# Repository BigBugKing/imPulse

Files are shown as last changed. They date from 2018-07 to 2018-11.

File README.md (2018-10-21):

# Important Notice
This is an open project, so...WORK IN PROGRESS! You might find bugs and incomplete work all over this repository. Therefore, I kindly ask you to keep calm and inform me if you encounter any issue. Thank you!

This project is licensed under the terms of the GNU General Public License v3.0

# What is imPulse?
Energy harvesting alternative for bikes including data logging, smart illumination system and Power Distribution Board for powerbanks

# Description

The aim of this project is to provide a cost-effective alternative to power generation on bikes using conventional stepper motors while adding other capabilities, such as: 

- An integrated data logging system to monitor power generated on each trip. 

- A smart lighting system with addressable LEDs, working as indicators, braking lights and headlights, incorporating Light Dependant Resistors (LDRs) to sense the environment and to reduce the risk of glare. 

- Power Distribution Board (PDB) to charge two different/generic powerbanks. While one powerbank is charged, the other one is used to supply energy to the system. 

Please bear in mind that I am currently testing quick prototypes that may compromise the bike reliability in some cases (aka 'learn by doing'). No stress, compression, bending or torsion analysis have been carried out yet on the power generation stage, so use all this project content at your own risk. 

# Milestones for Hackaday 2018

- Power Generation Stage (Closed)
- Data Logger Stage (Closed)
- Smart Lighting System (Closed)
- eBox Stage (Closed)
- Wiring Harness Stage (Closed)

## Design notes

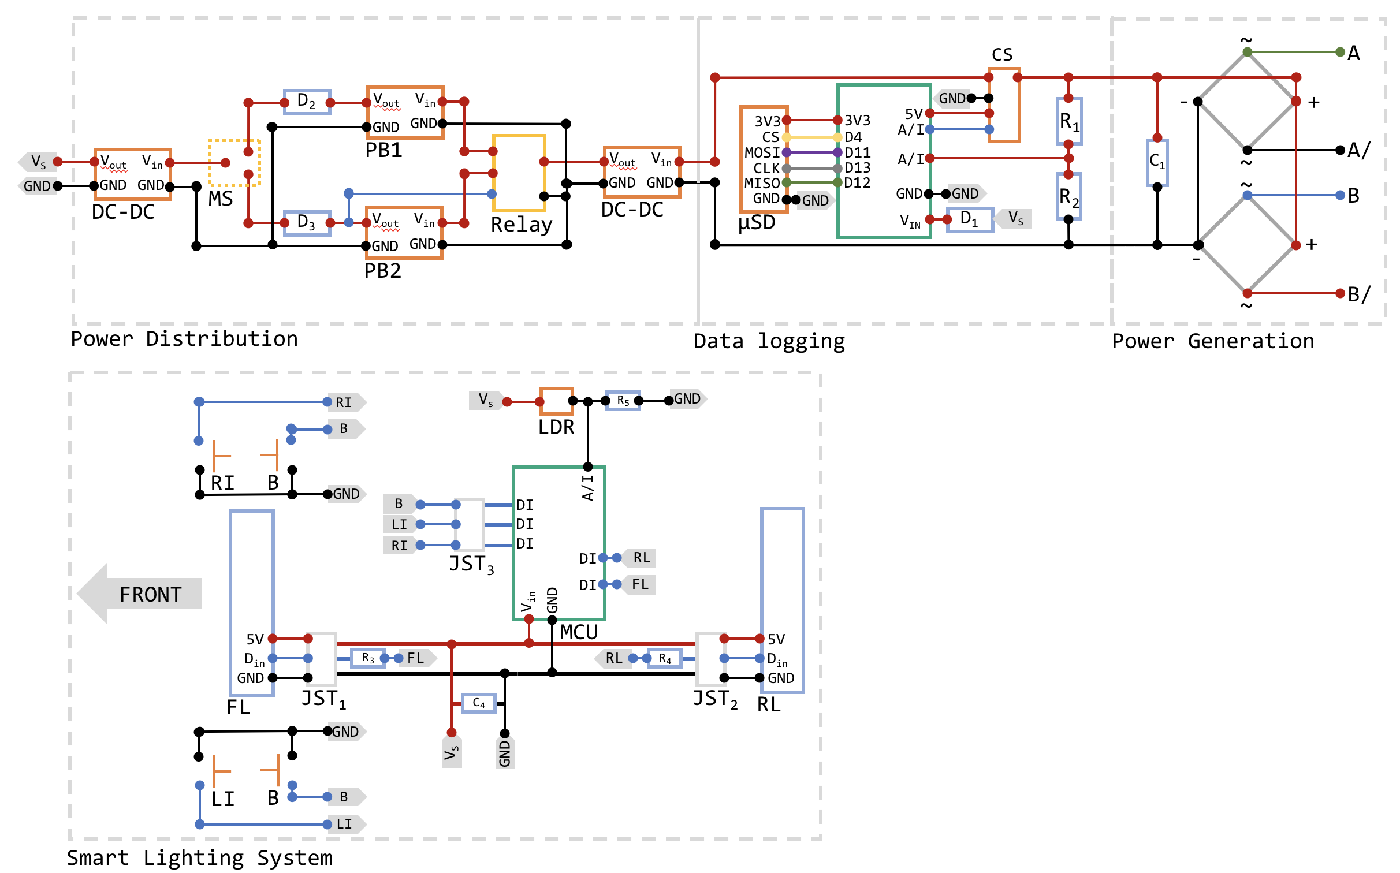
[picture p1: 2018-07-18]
Diagrams/SystemIntegrationStage_v1.png

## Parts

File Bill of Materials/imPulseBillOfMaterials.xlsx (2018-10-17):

Power Generation Stage
Item | Description | Company | Price/Unit | Units | Total | Total + VAT
Stepper Motor | Nema 17 2 Phase 4-wire Stepper Motor 1.8 Degree for 3D Printer (42 x 42 x 34mm) (https://www.amazon.co.uk/Phase-4-wire-Stepper-Degree-Printer/dp/B06ZY9G8KG) | Amazon | £9.16 | 1 | £9.16 | £10.99
JSP XPH-4 | 2.54mm JST-XHP 2 / 3 / 4 / 5 Pin housing and Male / Female Pin Head Connector Adapter Plug (600pcs) (https://www.amazon.co.uk/gp/product/B01GZKFML0/ref=oh_aui_detailpage_o00_s00?ie=UTF8&psc=1) | Amazon | £0.02 | 6 | £0.12 | £0.15
M3 screw | M2 M3 M4 Stainless Steel Hex Head Set Screw Bolts and Nuts (1080pcs) (https://www.ebay.co.uk/itm/1080PC-Assortment-M2-M3-M4-Stainless-Steel-Hex-Head-Set-Screw-Bolts-and-Nuts-Kit/263923485964) | eBay | £0.01 | 4 | £0.04 | £0.05
U channel | Aluminium 6000 U Channel (5m length,38.1x19.1x3.2mm) (20cm needed) (https://www.metalswarehouse.co.uk/product/aluminium-channel/?attribute_pa_grade=6000-series) | Metals Warehouse | £0.90 | 1 | £0.75 | £0.90
Spur Gear | 3D-printed Spur Gear (Cost based on Zortrax Suite) | N/A | 0.66 | 1 | £0.66 | £0.66
Pinion Gear | 3D-printed Pinion Gear (Cost based on Zortrax Suite) | N/A | 0.09 | 1 | £0.09 | £0.09
Washer | A2 Stainless Steel M6 washer (10pcs) (https://www.ebay.co.uk/itm/FORM-C-WASHERS-A2-STAINLESS-STEEL-M4-M5-M6-M8-M10-M12-WIDER-LARGER-FLAT-WIDE-RIM/150939016233) | eBay | £0.11 | 6 | £0.68 | £0.81
Full-wave rectifier | Full Wave Bridge Rectifier 2W08M (2pcs) (https://www.ebay.co.uk/itm/W02M-200V-1A-Full-Wave-Bridge-Rectifier-W02M/191971165883) | eBay | £1.65 | 2 | £3.29 | £3.95
Capacitor | 100uF 25v 105c Low ESR (10pcs) (https://www.ebay.co.uk/itm/100uf-25v-105c-LOW-ESR-Size-11-2mmx6mm-Panasonic-EEUFM1E101-x10pcs/301203555992) | eBay | £0.20 | 1 | £0.20 | £0.24
DC-DC converter | DC 6-24V 12V 24V to 5V 3A USB Step Down Converter (https://www.ebay.co.uk/itm/DC-6-24V-12V-24V-to-5V-3A-Car-USB-Charger-Module-Buck-Step-Down-Converter-Phone/401265883616) | eBay | £2.91 | 1 | £2.91 | £3.49
M3 Grub Screw | M3 A2 Steel Allen Grub Screw (M3x3mm) (4pcs) (https://www.ebay.co.uk/itm/360511046069) | eBay | £0.21 | 1 | £0.21 | £0.25
Data Logging Stage
Item | Description | Company | Price/Unit | Units | Total | Total + VAT
MCU | FireBeetle ESP32 IOT Microcontroller (https://shop.pimoroni.com/products/firebeetle-esp32-iot-microcontroller-supports-wi-fi-bluetooth) | Pimoroni | £15.83 | 1 | £15.83 | £19.00
Current Sensor | 30A ACS712 Current Sensor Module (https://www.ebay.co.uk/itm/5A-20A-30A-ACS712-Module-Measuring-Range-Current-Sensor-Hall-Board-Arduino-PI/262759555611) | eBay | £2.67 | 1 | £2.67 | £3.20
Resistor | Carbon Film Resistor (1 KOhm, 1/4W, 0.25W) (10pcs) (https://www.ebay.co.uk/itm/Carbon-Film-Resistors-1-4W-0-25W-Full-Range-of-Values-Various-Pack-Sizes/152059712084) | eBay | £0.04 | 1 | £0.04 | £0.05
Resistor | Carbon Film Resistor (120 Ohm, 1/4W, 0.25W) (10pcs) (https://www.ebay.co.uk/itm/Carbon-Film-Resistors-1-4W-0-25W-Full-Range-of-Values-Various-Pack-Sizes/152059712084) | eBay | £0.04 | 1 | £0.04 | £0.05
Smart Lighting System Stage
LED Matrix | WS2812B Black LED, WS2811 IC Built-in, 5050 SMD, RGB, DC5V (100pcs) (https://www.amazon.co.uk/gp/product/B01DC0J3UM/ref=od_aui_detailpages00?ie=UTF8&psc=1) | Amazon | £15.57 | 1 | £15.57 | £18.68
LDR | GL5528 Light Dependent Resistor/Photoresistor (10pcs) (https://www.ebay.co.uk/itm/10x-LDR-5528-GL5528-Light-Dependent-Resistor-Photoresistor/132685567359) | eBay | £0.08 | 3 | £0.25 | £0.30
Front Light | 3D-printed Front Light Assembly (Cost based on Zortrax Suite) | N/A | £2.94 | 1 | £2.94 | £2.94
Rear Light | 3D-printed Rear Light Assembly (Cost based on Zortrax Suite) | N/A | £1.28 | 1 | £1.28 | £1.28
M3 screw | M2 M3 M4 Stainless Steel Hex Head Set Screw Bolts and Nuts (1080pcs) (https://www.ebay.co.uk/itm/1080PC-Assortment-M2-M3-M4-Stainless-Steel-Hex-Head-Set-Screw-Bolts-and-Nuts-Kit/263923485964) | eBay | £0.01 | 10 | £0.10 | £0.12
JSP XPH-3 | 2.54mm JST-XHP 2 / 3 / 4 / 5 Pin housing and Male / Female Pin Head Connector Adapter Plug (600pcs) (https://www.amazon.co.uk/gp/product/B01GZKFML0/ref=oh_aui_detailpage_o00_s00?ie=UTF8&psc=1) | Amazon | £0.02 | 15 | £0.31 | £0.37
eBox Stage
Item | Description | Company | Price/Unit | Units | Total | Total + VAT
eBox | 3D-printed eBox Assembly(Cost based on Zortrax Suite) | N/A | £3.50 | 1 | £3.50 | £3.50
Power Bank Housing | 3D-printed Power Bank Housing Assembly (Cost based on Zortrax Suite) | N/A | £2.01 | 2 | £4.02 | £4.02
Mounting Bracket | 3D-printed unting Bracket (Cost based on Zortrax Suite) | N/A | £2.38 | 1 | £2.38 | £2.38
Stripboard | Vero PCB Prototyping Board, Strip Board (95x127mm) (https://www.ebay.co.uk/itm/Vero-PCB-Prototyping-Stripboard-Strip-Board-2-54mm-Pitch/282567751352) | eBay | £1.99 | 1 | £1.99 | £2.39
Relay | 5V Mini Songle Relay SPDT 5-Pins PCB (https://www.ebay.co.uk/itm/5V-12V-24V-Mini-Songle-Relay-SPDT-5-Pins-PCB-1st-Class/281769556517) | eBay | £1.24 | 1 | £1.24 | £1.49
Diode | 1N4007 1000V 1A General Purpose Diodes (10pcs) (https://www.ebay.co.uk/itm/10-x-1N4007-1000v-1A-General-Purpose-Diodes-IN4007-1N4000-DO41-UK-Free-Postage/132541781407) | eBay | £0.08 | 2 | £0.17 | £0.20
USB cable | USB 2.0 to MICRO USB Male / Male cable, 1m | eBay | £0.83 | 2 | £1.65 | £1.98
Power Bank | Ultra Slim Emergency Pocket Sized Battery Power Bank (2000mAh, 1A@5V) (https://www.amazon.co.uk/gp/product/B01KN1OV5K/ref=oh_aui_detailpage_o02_s00?ie=UTF8&psc=1) | Amazon | £8.33 | 2 | £16.65 | £19.98
Single Solid Core (SSC) Wire | Black Single Solid Core 1.8A@300V, 22-23 AWG (0.6mm x 1m) (https://www.ebay.co.uk/itm/13m-1-0-6mm-Equipment-Wire-Kit-22-23-AWG-Single-Solid-Core-1-8A-WP-011118/232901568073) | eBay | £0.22 | 1 | £0.22 | £0.26
SSC Wire | Red Single Solid Core 1.8A@300V, 22-23 AWG (0.6mm x 1m) (https://www.ebay.co.uk/itm/13m-1-0-6mm-Equipment-Wire-Kit-22-23-AWG-Single-Solid-Core-1-8A-WP-011118/232901568073) | eBay | £0.22 | 1 | £0.22 | £0.26
SSC Wire | Green Single Solid Core 1.8A@300V, 22-23 AWG (0.6mm x 1m) (https://www.ebay.co.uk/itm/13m-1-0-6mm-Equipment-Wire-Kit-22-23-AWG-Single-Solid-Core-1-8A-WP-011118/232901568073) | eBay | £0.22 | 1 | £0.22 | £0.26
SSC Wire | Yellow Single Solid Core 1.8A@300V, 22-23 AWG (0.6mm x 1m) (https://www.ebay.co.uk/itm/13m-1-0-6mm-Equipment-Wire-Kit-22-23-AWG-Single-Solid-Core-1-8A-WP-011118/232901568073) | eBay | £0.22 | 1 | £0.22 | £0.26
SSC Wire | Orange Single Solid Core 1.8A@300V, 22-23 AWG (0.6mm x 1m) (https://www.ebay.co.uk/itm/13m-1-0-6mm-Equipment-Wire-Kit-22-23-AWG-Single-Solid-Core-1-8A-WP-011118/232901568073) | eBay | £0.22 | 1 | £0.22 | £0.26
SSC Wire | Purple Single Solid Core 1.8A@300V, 22-23 AWG (0.6mm x 1m) (https://www.ebay.co.uk/itm/13m-1-0-6mm-Equipment-Wire-Kit-22-23-AWG-Single-Solid-Core-1-8A-WP-011118/232901568073) | eBay | £0.22 | 1 | £0.22 | £0.26
M3 screw | M2 M3 M4 Stainless Steel Hex Head Set Screw Bolts and Nuts (1080pcs) (https://www.ebay.co.uk/itm/1080PC-Assortment-M2-M3-M4-Stainless-Steel-Hex-Head-Set-Screw-Bolts-and-Nuts-Kit/263923485964) | eBay | £0.01 | 2 | £0.02 | £0.02
Rubber Sheet | Rubber Sheet (250 x 250 x 1.5mm) (https://www.ebay.co.uk/itm/RUBBER-SHEET-VARIOUS-SIZES-X-1MM-TO-25MM-THICKNESS-AVAILABLE/141120177410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) | eBay | £2.33 | 1 | £2.33 | £2.80
M3 Insert | M3 Threaded Brass Insert for Plastic (M3 x 4.1mm) (5pcs) (https://www.ebay.co.uk/itm/THREADED-BRASS-INSERTS-FOR-PLASTIC-SOLID-PRESS-FIT-METRIC-BARBED-M2-M3-M4-M5-M6/192514339545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) | eBay | £0.25 | 2 | £0.50 | £0.60
Magnet Disc | Neodynium Magnet Disc (25pcs) (https://www.ebay.co.uk/itm/Neodymium-Magnets-Super-Strong-Rare-Earth-Magnets-Craft-Disc-N35-N52-3mm-20mm/253320715735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) | eBay | £0.08 | 8 | £0.64 | £0.76
Rod Bar | DIY Model Stainless Steel Round Rod Bar (2x200mm) (2pcs) (https://www.amazon.co.uk/gp/product/B00O9Y1ENA/ref=oh_aui_detailpage_o08_s00?ie=UTF8&psc=1) | Amazon | £1.28 | 1 | £1.28 | £1.54
LED | LED's Pack in Blue, Green, Yellow and White (100pcs) (https://www.ebay.co.uk/itm/5mm-LEDS-Pack-OF-100-20x-Each-of-Red-Blue-Green-Yellow-White-UK-Seller/182307853772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) | eBay | £0.02 | 2 | £0.04 | £0.05
Resistor | Carbon Film Resistor (220 Ohm, 1/4W, 0.25W) (10pcs) (https://www.ebay.co.uk/itm/Carbon-Film-Resistors-1-4W-0-25W-Full-Range-of-Values-Various-Pack-Sizes/152059712084) | eBay | £0.04 | 2 | £0.08 | £0.10
Switch | Heavy Duty ON/OFF/ON Toggle Switch DPDT + Water Cover (https://www.ebay.co.uk/itm/Heavy-Duty-Toggle-Switch-Flick-ON-OFF-ON-Car-Dash-12V-DPDT-Missile-Water-Cover/371767136221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) | eBay | £2.33 | 1 | £2.33 | £2.79
Wiring Stage
Item | Description | Company | Price/Unit | Units | Total | Total + VAT
Heat Shrink | Black Heat Shrink Tube 3:1 with glue (10mm x 1m) (https://www.amazon.co.uk/gp/product/B06WGQMB1Z/ref=oh_aui_detailpage_o00_s00?ie=UTF8&psc=1) | Amazon | £5.83 | 1 | £5.83 | £6.99
Heat Shrink | Black Heat Shrink Tube 3:1 with glue (5mm x 1m) (https://www.amazon.co.uk/gp/product/B06X3WJ894/ref=oh_aui_detailpage_o00_s00?ie=UTF8&psc=1) | Amazon | £3.33 | 2 | £6.66 | £7.99
Silicon Wire | Black Flexible Soft Silicone Wire Cable 22 AWG (5m) (https://www.ebay.co.uk/itm/Flexible-Soft-Silicone-Wire-Cable-10-12-14-16-18-20-22-24-26-28-30-AWG/322860010747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) | eBay | £1.92 | 2 | £3.83 | £4.60
Silicon Wire | Red Flexible Soft Silicone Wire Cable 22 AWG (5m) (https://www.ebay.co.uk/itm/Flexible-Soft-Silicone-Wire-Cable-10-12-14-16-18-20-22-24-26-28-30-AWG/322860010747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) | eBay | £1.92 | 2 | £3.83 | £4.60
Silicon Wire | Blue Flexible Soft Silicone Wire Cable 22 AWG (5m) (https://www.ebay.co.uk/itm/Flexible-Soft-Silicone-Wire-Cable-10-12-14-16-18-20-22-24-26-28-30-AWG/322860010747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) | eBay | £1.92 | 1 | £1.92 | £2.30
Cable ties | Strong Nylon Plastic Cable Ties Zip, Tie Wraps Organizer (200mm x4.8mm) (100pcs) (https://www.ebay.co.uk/itm/200mmStrong-Nylon-Plastic-Cable-Ties-Zip-Tie-Wraps-organizer-4-8mm-Black-100pcs/391121204862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) | eBay | £1.66 | 1 | £1.66 | £1.99
Cable ties | Releasable Cable Ties, Zip Wrap Straps (100mm x 3.6mm)(100pcs) (https://www.amazon.co.uk/gp/product/B01KK0CAMU/ref=oh_aui_detailpage_o00_s00?ie=UTF8&psc=1) | Amazon | £2.49 | 1 | £2.49 | £2.99
 |  |  |  |  | Total: | £145.20

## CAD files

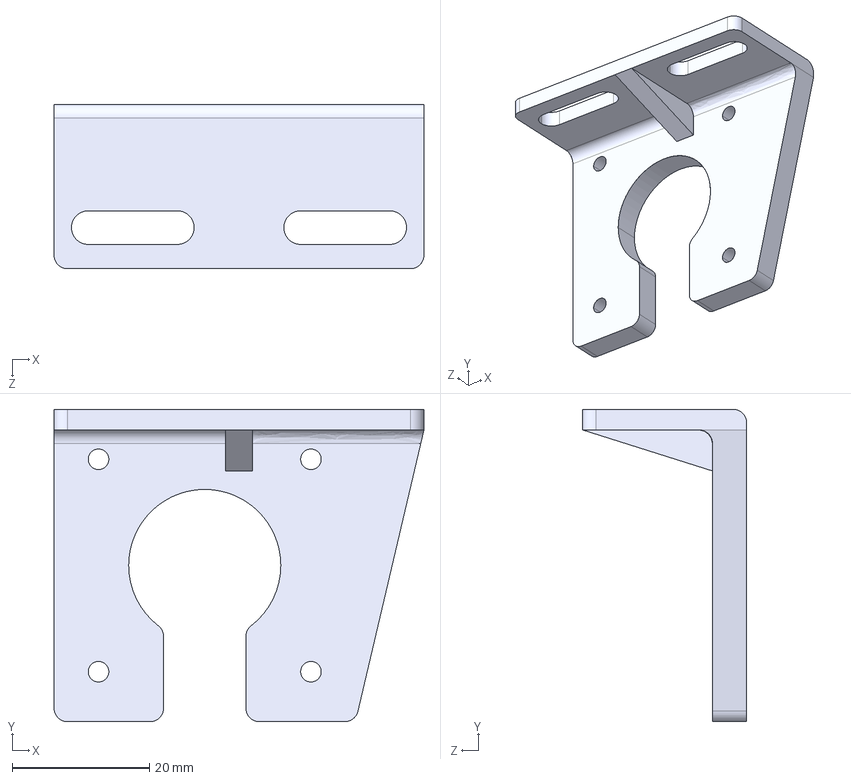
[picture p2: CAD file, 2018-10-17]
CAD/partStepperBracketPlastic.IGS
54.0 x 45.6 x 24.0 mm

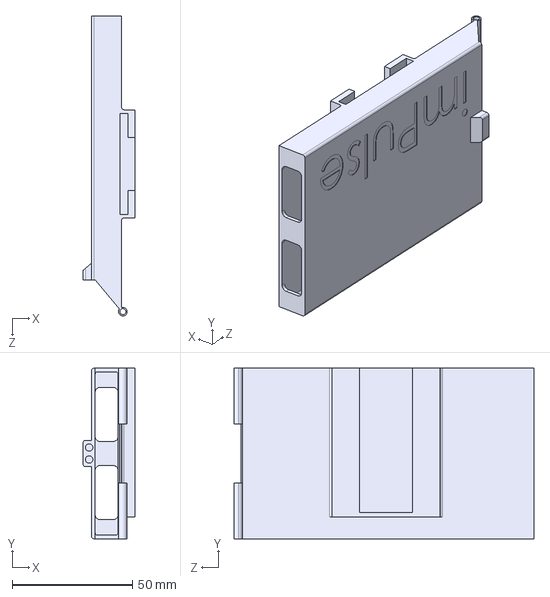
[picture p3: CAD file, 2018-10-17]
CAD/parteBoxBatteryHolderRight.IGS
21.5 x 71.0 x 124.8 mm

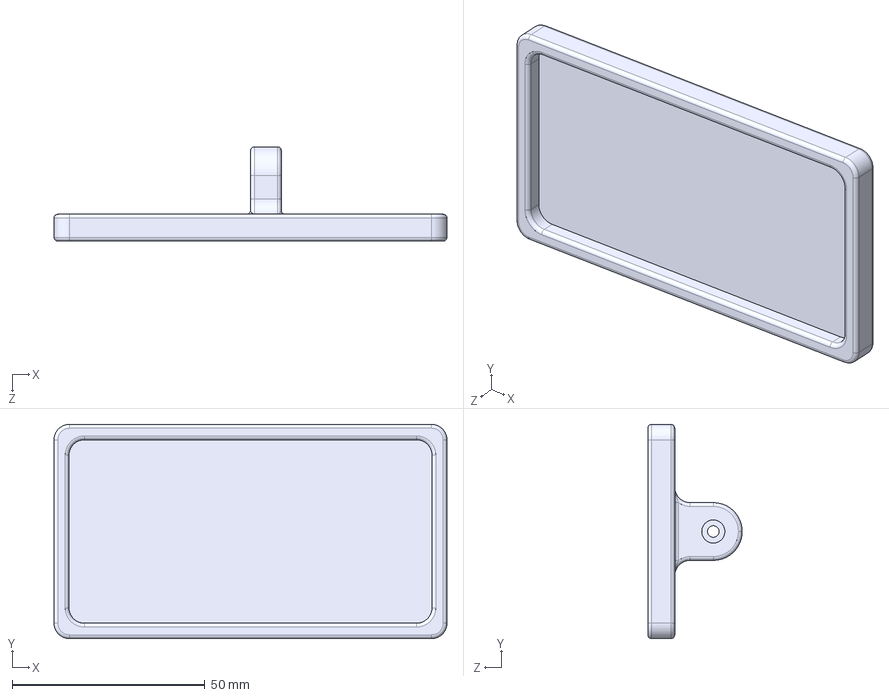
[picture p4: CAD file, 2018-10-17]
CAD/partRearlight.IGS
102.0 x 55.6 x 24.5 mm

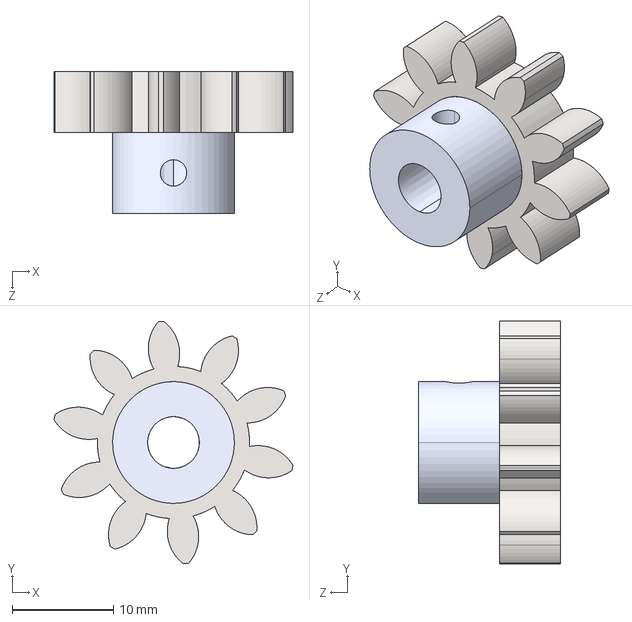
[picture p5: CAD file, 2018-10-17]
CAD/partPinionCustomManufacture.IGS
23.6 x 23.9 x 14.0 mm

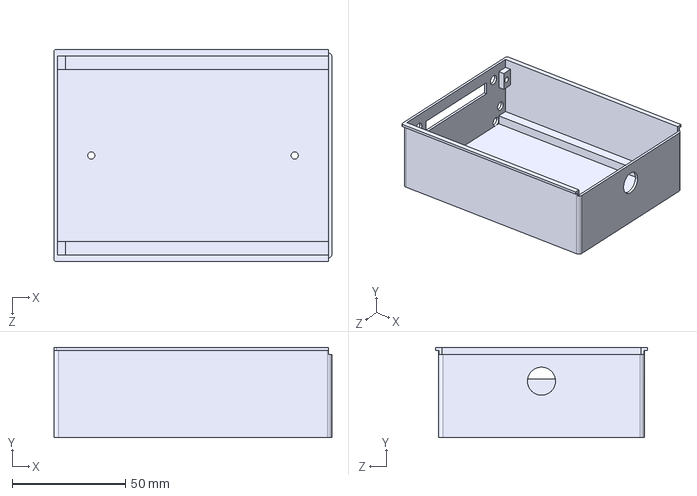
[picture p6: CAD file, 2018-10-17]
CAD/parteBox.IGS
123.0 x 40.0 x 94.0 mm

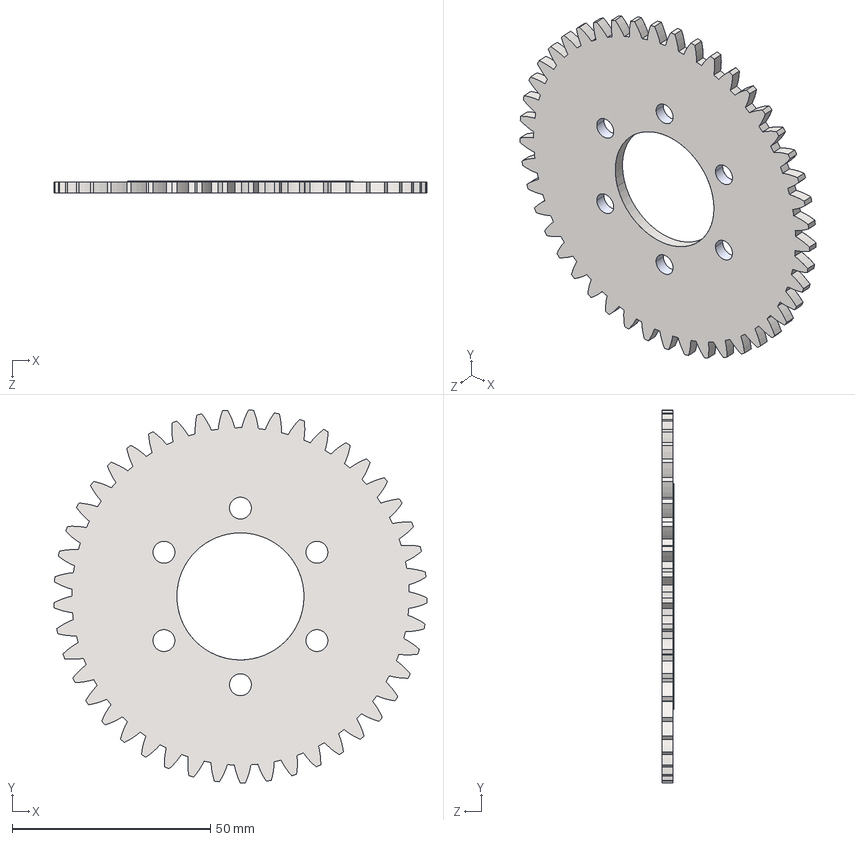
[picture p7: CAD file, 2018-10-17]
CAD/partSpurCustomReinforced.IGS
94.0 x 94.0 x 3.00 mm

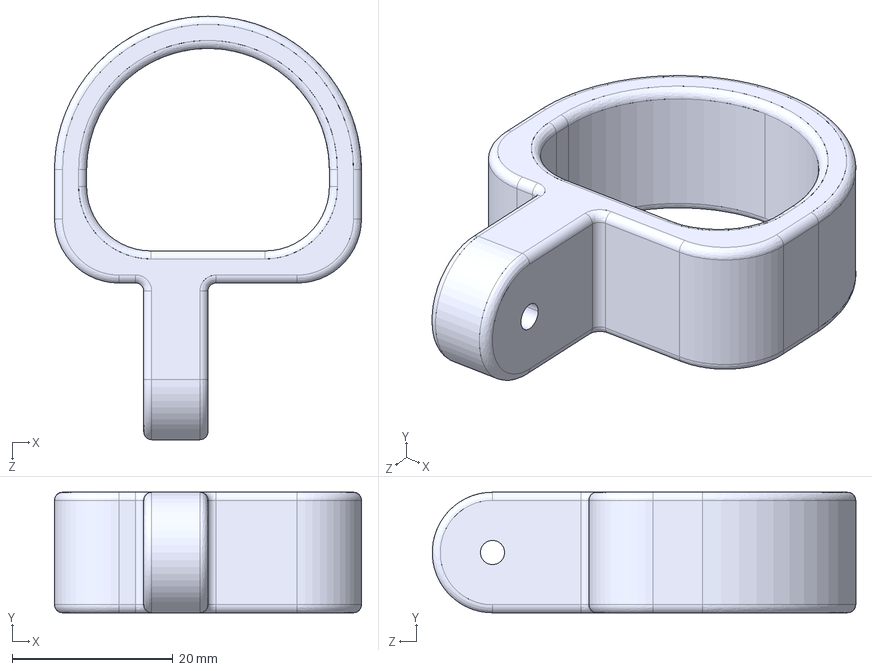
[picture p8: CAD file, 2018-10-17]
CAD/partRearLightSupport.IGS
38.2 x 15.0 x 52.7 mm

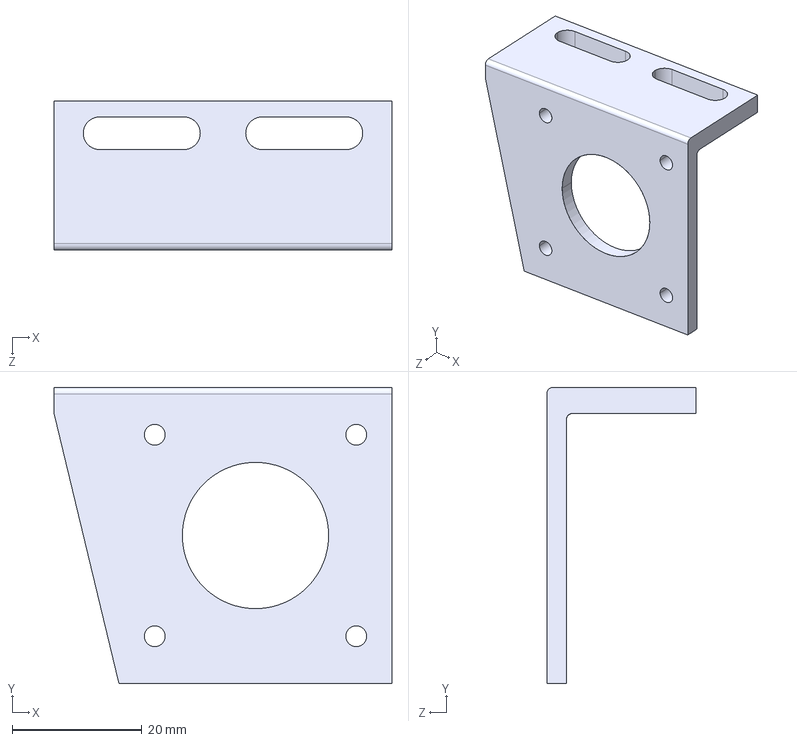
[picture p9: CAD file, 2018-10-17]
CAD/partStepperBracketAl.IGS
52.0 x 45.6 x 23.0 mm

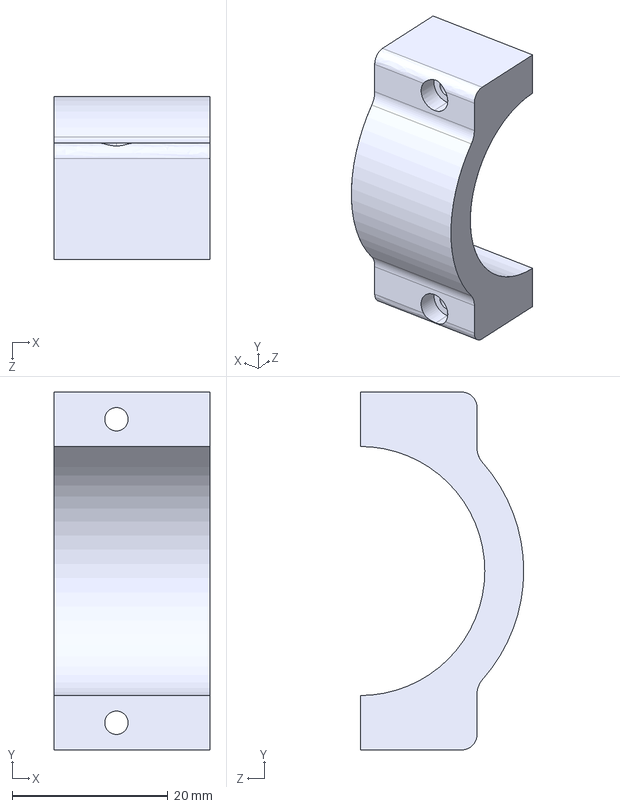
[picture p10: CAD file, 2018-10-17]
CAD/partHeadlightBracket.IGS
20.0 x 46.0 x 21.0 mm

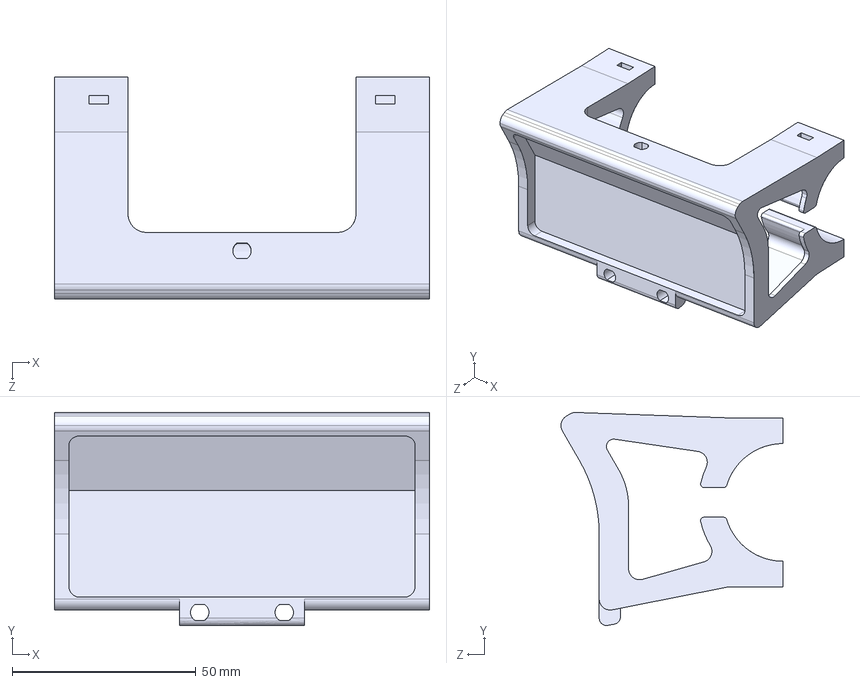
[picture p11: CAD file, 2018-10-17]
CAD/partHeadlight.IGS
102.0 x 58.0 x 60.4 mm

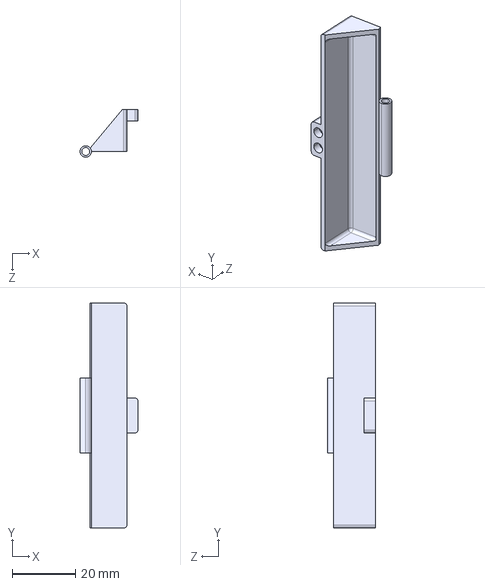
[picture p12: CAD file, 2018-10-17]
CAD/parteBoxBatteryHolderkLid.IGS
18.3 x 71.0 x 15.0 mm

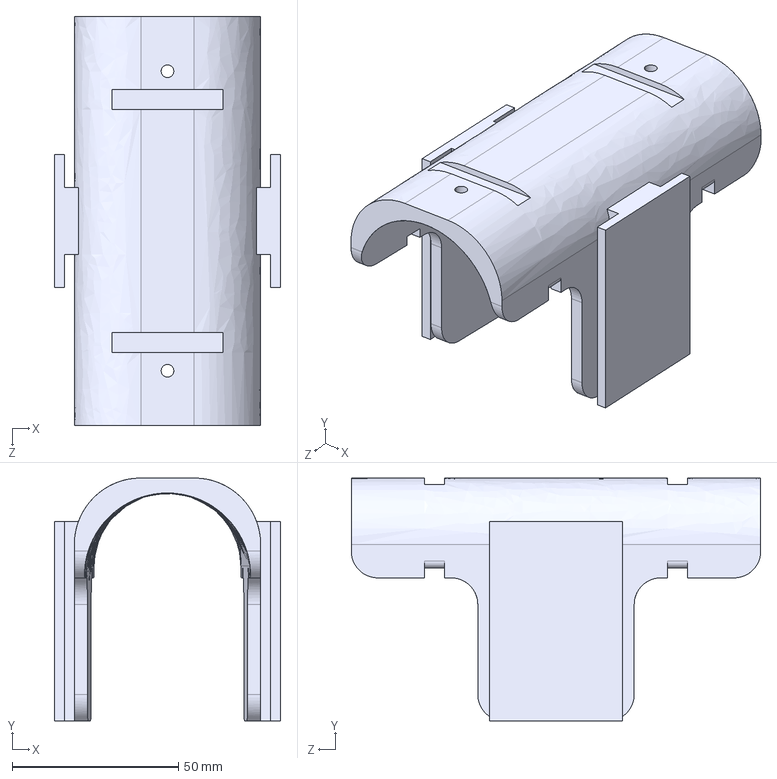
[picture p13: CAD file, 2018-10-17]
CAD/parteBoxMountingBracket.IGS
68.0 x 73.0 x 123.0 mm

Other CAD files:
CAD/parteBoxBatteryHolderLeft.IGS

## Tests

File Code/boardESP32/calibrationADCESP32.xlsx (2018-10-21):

Real voltage [V] | ADC Raw [div]
0.152 | 19
0.201 | 79
0.301 | 200
0.401 | 320
0.501 | 439
0.601 | 563
0.7 | 685
0.801 | 805
0.901 | 927
1 | 1054
1.1 | 1174
1.2 | 1297
1.301 | 1421
1.4 | 1535
1.5 | 1665
1.6 | 1788
1.7 | 1906
1.8 | 2030
1.9 | 2154
2 | 2274
2.1 | 2394
2.2 | 2515
2.3 | 2642
2.4 | 2768
2.5 | 2897
2.6 | 3038
2.7 | 3199
2.8 | 3374
2.9 | 3566
3 | 3782
3.1 | 4015
3.14 | 4095

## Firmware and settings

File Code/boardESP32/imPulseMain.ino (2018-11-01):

/*  This program will manage all your bike sub-systems...bECU!
 *  Author: Javier Betancor
 *  Project: imPulse
 *  Version: 0.0.2 - 30/10/18
 *  Libraries/packages needed: FireBeetle driver, VCP driver for MAC, arduino-esp32, 
 *    sudo easy_install pip, python -m pip install pyserial FastLED 3.2.1, 
 *    Blynk 0.5.4, ESP_BLE_Arduino 0.4.16
 */

/*---------- LIBRARIES ----------*/

/*----- Smart Lighting System -----*/

//#define FASTLED_INTERRUPT_RETRY_COUNT 0 //Just in case -- Ref: https://github.com/FastLED/FastLED/issues/306
#define FASTLED_ALLOW_INTERRUPTS 0 //Ref: https://github.com/FastLED/FastLED/issues/306
#include "FastLED.h"

/*----- Blynk -----*/

//#define BLYNK_PRINT Serial //Comment this out to disable prints and save space

#define BLYNK_USE_DIRECT_CONNECT

#include <BlynkSimpleEsp32_BLE.h>
#include <BLEDevice.h>
#include <BLEServer.h>


/*---------- PINS/VARIABLES DEFINITION ----------*/

/*----- Smart Lighting System -----*/

#define NUM_LEDS 50 //LEDs in your strip for both lights as they have the same number of LEDs
#define NUM_STRIPS 2 //No. of independent strips (Front Light + Rear Light = 2)
#define R_DATA_PIN 2// D9 (IO02) - Data pin for WS281B RGB LED type for rear light
#define F_DATA_PIN 13// D7 (IO13) - Data pin for WS281B RGB LED type for front light
CRGB Rleds[NUM_LEDS]; //Define the array of LEDs
CRGB Fleds[NUM_LEDS]; //Define the array of LEDs

portMUX_TYPE mux = portMUX_INITIALIZER_UNLOCKED;

const byte Brake = 25;//D2 (IO25) - Brake Pin
bool stateBrake = HIGH; //Brake Light boolbean state
bool stateBeam = HIGH; //Beam Light boolbean state
int ambLight = 0; //Initialize LDR varioable for analog readings
int LI = 5;// D8 (IO05) - Left Indicator Pin
int RI = 27;// D4 (IO27) - Right Indicator Pin
volatile int countL = 1; //Count for LI needs to be volatile
volatile int countR = 1; //Count for RI needs to be volatile
long delayTime = 0;

const byte topLDR = 39; // A1 (IO39) - Top LDR
//const byte rightLDR = 34 ; // A2 (IO34) - Rigth LDR
//const byte leftLDR = 36; // A0 (IO36) - Left LDR

/*----- DATA LOGGER -----*/
int sensorCurrent = 35; //A3 (IO35) for current sensor
int sensorVoltage = 15; //A4 (IO15) for voltage sensor
float conv = 0.0153;//(4141/4096)*(1/66); TUNE when PoweBank is connected. Low value because of the Diode (5-0.7) = 4.3V
int iter = 50; //Number of iterations
double sum = 0; //Number of total readings 

/*----- Blynk -----*/
WidgetLED ledBrake(V4);//Brake light in Blynk
WidgetLED ledRightInd(V5);//Right indicator in Blynk
WidgetLED ledLeftInd(V6);//Left indicator in Blynk
WidgetLED ledBeam(V7);//Beam light in Blynk
float linearSpeed = 0;
char auth[] = "d5c5166f65a44eea86f942b742dc9935"; //Blynk App auth. token


/*---------- OTHER FUNCTIONS ----------*/

/*----- Smart Lighting System -----*/

// Left Indicator Pressed Interrupt Service Routine (ISR) for ESP32
// Ref: https://techtutorialsx.com/2017/09/30/esp32-arduino-external-interrupts/
void IRAM_ATTR LIP (){ 
  portENTER_CRITICAL_ISR(&mux);
  if (digitalRead (LI) == LOW){
    countL++;
  }
  portEXIT_CRITICAL_ISR(&mux);
}  // End of LIP

// Right Indicator Pressed ISR
void IRAM_ATTR RIP (){
  portENTER_CRITICAL_ISR(&mux);
  if (digitalRead (RI) == LOW){
    countR++;
  }
  portEXIT_CRITICAL_ISR(&mux);
}  // End of RIP

/*----- Blynk -----*/

BLYNK_WRITE(V1){ //Get linear speed from phone
  GpsParam gps(param);
  linearSpeed = gps.getSpeed();
}

BLYNK_READ(V2){ //Send linear speed to Blynk
  Blynk.virtualWrite(V2, linearSpeed);
}

BLYNK_READ(V3){ //Send power generated to Blynk
  
  float amps = (trueVoltage(sensorCurrent)-2.076)*conv;//2.161V measured with Vmeter across OUT and GND pins of the ACS71230A
  float volts = readSensor(sensorVoltage)/11.872; //Spreadsheed trend line
  float powGen = abs(volts/10*amps); // P = V*I [W] NEED CHANGES
  Blynk.virtualWrite(V3, powGen);
}


void setup (){
  
  /*----- Smart Lighting System -----*/
  
  FastLED.addLeds<WS2812B, R_DATA_PIN, GRB>(Rleds, NUM_LEDS); //Add rear LEDs to stripe 0
  FastLED.addLeds<WS2812B, F_DATA_PIN, GRB>(Fleds, NUM_LEDS); //Add front LEDs to stripe 1
  pinMode(LI, INPUT_PULLUP);
  pinMode(RI, INPUT_PULLUP);
  pinMode(Brake, INPUT_PULLUP);
  pinMode(topLDR, INPUT);
  //pinMode(rightLDR, INPUT);
  //pinMode(leftLDR, INPUT);
  attachInterrupt (digitalPinToInterrupt (LI), LIP, CHANGE); //LI interrupt
  attachInterrupt (digitalPinToInterrupt (RI), RIP, CHANGE); //RI interrupt
  //Serial.begin(9600);

  /*----- DATA LOGGER -----*/
  pinMode(sensorCurrent,INPUT);
  pinMode(sensorVoltage,INPUT);

  /*----- Blynk -----*/
  Blynk.setDeviceName("imPulse");
  Blynk.begin(auth);
  
 
  //Startup protocol? -- FUTURE RELEASE
  
}  // End of setup

void loop (){
  
  /*----- Smart Lighting System -----*/

  //Brake light condition does not depend on LDR values
  if (digitalRead(Brake) == LOW){
    
    brakeLight(50);
    stateBrake = LOW;
    
  } else if (digitalRead(Brake)== HIGH && stateBrake == LOW){
    
    brakeOff();
    stateBrake = HIGH;
    
  }

  ambLight = analogRead(topLDR);

  //Beam Light condition
  if (ambLight <= 100){
    
    headLightOn(50);
    brakeLight(20);
    stateBeam = LOW;
    delayTime = millis();
    
  } else if (ambLight > 100 && millis() - delayTime >= 5E3 && stateBeam == LOW){
    
    lightsOff();
    stateBeam = HIGH;
    ledBrake.off();
    ledBeam.off();
    
  }
  //Indicators' condition
  if(countR%2 == 0){
   
    indicatorOn(1,1);
      
  }else if(countL%2 == 0){
    
    indicatorOn(0,-1);
    
  }
  
  /*----- Blynk -----*/

  Blynk.run();

} //End of loop

/*----------  CUSTOM FUNCTIONS ----------*/

/*----- Smart Lighting System -----*/

//indicatorOn
void indicatorOn(int z,int j) {
  FastLED.setBrightness(50);
  for (int i = 0; i<=5;i++){

    //Front Light
    Fleds[(5-z)-i*j].setRGB(255,30,0);
    Fleds[(14+z)+i*j].setRGB(255,30,0);
    Fleds[(25-z)-i*j].setRGB(255,30,0);
    Fleds[(34+z)+i*j].setRGB(255,30,0);
    Fleds[(45-z)-i*j].setRGB(255,30,0);

    //Rear Light
    Rleds[(5-z)+i*j].setRGB(255,30,0);
    Rleds[(14+z)-i*j].setRGB(255,30,0);
    Rleds[(25-z)+i*j].setRGB(255,30,0);
    Rleds[(34+z)-i*j].setRGB(255,30,0);
    Rleds[(45-z)+i*j].setRGB(255,30,0);
    FastLED.show();
    delay (80); 
  }
  delay(200);

  if(z == 1 && j == 1){ledRightInd.on();}else{ledLeftInd.on();}

  fill_solid(Fleds, NUM_LEDS, CRGB::Black);
  fill_solid(Rleds, NUM_LEDS, CRGB::Black);
  FastLED.show();

    if(z == 1 && j == 1){ledRightInd.off();}else{ledLeftInd.off();}
}//End of indicatorOn

//lightsOff
void lightsOff(){
  fill_solid(Fleds, NUM_LEDS, CRGB::Black);
  fill_solid(Rleds, NUM_LEDS, CRGB::Black);
  FastLED.show();
  ledBrake.off();
  ledBeam.off();
} //End of lightsOff

//brakeLight
void brakeLight(int y){
  fill_solid(Rleds, NUM_LEDS, CRGB::Red);
  FastLED[0].showLeds(y);
  ledBrake.on();
}//End of brakeLight

//brakeOff
void brakeOff(){
  fill_solid(Rleds, NUM_LEDS, CRGB::Black);
  FastLED.show();
  ledBrake.off();
} //End of brakeOff

//headLightOn
void headLightOn(int k){
  fill_solid(Fleds, NUM_LEDS, CRGB::White);
  FastLED[1].showLeds(k);
  ledBeam.on();
}//End of HeadLightOn


/*----- DATA LOGGER -----*/

double readSensor(byte sensor) {
  sum = 0;
  for (int j = 0; j < iter; j++) {
    sum += analogRead(sensor);
    delay(7);
  }
  return sum;
}

double trueVoltage(byte pin){
  sum = 0;
  for (int j = 0; j < iter; j++) {
    sum += analogRead(pin);
    delay(7);
  }
  sum = sum/iter;
  if(sum < 1 || sum > 4095) return 0;
  return -6E-15*pow(sum,4) + 3E-11*pow(sum,3) - 4E-8*pow(sum,2) + 0.0008*sum + 0.1367;//Check trendline for ESP32
  }

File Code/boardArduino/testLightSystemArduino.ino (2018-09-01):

/*
 * Reference: http://www.gammon.com.au/interrupts -- Amazing guy!! =) 
 */

#include "FastLED.h"

#define NUM_LEDS 50 //LEDs in your strip for both lights as they have the same number of LEDs
#define R_DATA_PIN 7//27 //Data pin for WS281B RGB LED type for rear light
#define F_DATA_PIN 6//26 //Data pin for WS281B RGB LED type for rear light
CRGB Rleds[NUM_LEDS]; //Define the array of LEDs
CRGB Fleds[NUM_LEDS]; //Define the array of LEDs

const byte Brake = 4; //Brake Pin
const byte LI = 2; //Left Indicator Pin
const byte RI = 3;//25; //Right Indicator Pin
volatile int countL = 1; //Count for LI
volatile int countR = 1; //Count for LI

//Add LDR (3)
const byte LDR1 = 1; //For ambient light
//const byte LDR2 = ;
//const byte LDR3 = ;



void setup (){
  
  FastLED.addLeds<WS2812B, R_DATA_PIN, GRB>(Rleds, NUM_LEDS); //Add rear LEDs
  FastLED.addLeds<WS2812B, F_DATA_PIN, GRB>(Fleds, NUM_LEDS); //Add front LEDs
  pinMode(LI, INPUT_PULLUP);
  pinMode(RI, INPUT_PULLUP);
  pinMode(Brake, INPUT_PULLUP);
  pinMode(LDR1, INPUT);
  //pinMode(LDR2, INPUT);
  //pinMode(LDR3, INPUT);
  attachInterrupt (digitalPinToInterrupt (LI), LIP, CHANGE); //LI interrupt
  attachInterrupt (digitalPinToInterrupt (RI), RIP, CHANGE); //RI interrupt

  //Startup strategy using only front lights with fade in/out and a funny face
  
}  // End of setup

void loop (){

  //Headlight condition
  int ambLight = analogRead(LDR1);
  if (ambLight <= 500){
    ambLight = map(ambLight,500,150,0,50); //Perhaps PID?
    headLightOn(ambLight);
    //brakeLight(20);//issues...CPU or way of programming?
    if (countL %2 == 0){
      indicatorOn(1,-1);
    }else if(countR %2 == 0){
      indicatorOn(0,1);
    }
    
  //Brake light condition
  }else if (ambLight <= 500 && digitalRead(Brake)==LOW){
    ambLight = map(ambLight,500,150,0,50);
    headLightOn(ambLight);
    //brakeLight(50);//issues...CPU or way of programming?
     if (countL %2 == 0){
      indicatorOn(1,-1);
    }else if(countR %2 == 0){
      indicatorOn(0,1);
    }
    
  }else if(digitalRead(Brake)==LOW){
    brakeLight(20);
    
  //Left indicator condition 
  }else if (countL %2 == 0){
    indicatorOn(0,-1);
    
  //Right indicator condition
  }else if(countR %2 == 0){
    indicatorOn(1,1);
  
  //Just keep lights off
  }else{
    lightsOff();
  }

} //End of loop

// Left Indicator Pressed Interrupt Service Routine (ISR)
void LIP (){
  if (digitalRead (LI) == LOW){
    countL++;
  }
}  // End of LIP

// Right Indicator Pressed ISR
void RIP (){
  if (digitalRead (RI) == LOW){
    countR++;
  }
}  // End of RIP


//indicatorOn
void indicatorOn(int z,int j) {
  FastLED.setBrightness(20);
  for (int i = 0; i<=5;i++){

    //Front Light
    Fleds[(5-z)-i*j].setRGB( 255, 30, 0);
    Fleds[(14+z)+i*j].setRGB( 255, 30, 0);
    Fleds[(25-z)-i*j].setRGB( 255, 30, 0);
    Fleds[(34+z)+i*j].setRGB( 255, 30, 0);
    Fleds[(45-z)-i*j].setRGB( 255, 30, 0);

    //Rear Light
    Rleds[(5-z)+i*j].setRGB( 255, 30, 0);
    Rleds[(14+z)-i*j].setRGB( 255, 30, 0);
    Rleds[(25-z)+i*j].setRGB( 255, 30, 0);
    Rleds[(34+z)-i*j].setRGB( 255, 30, 0);
    Rleds[(45-z)+i*j].setRGB( 255, 30, 0);
    FastLED.show();
    delay (70); 
  }
  delay(200);
  
  FastLED.setBrightness(20);
  for (int i = 0; i<=5;i++){

    //Front Light
    Fleds[(5-z)-i*j].setRGB( 0, 0, 0);
    Fleds[(14+z)+i*j].setRGB( 0, 0, 0);
    Fleds[(25-z)-i*j].setRGB( 0, 0, 0);
    Fleds[(34+z)+i*j].setRGB( 0, 0, 0);
    Fleds[(45-z)-i*j].setRGB( 0, 0, 0);

    //Rear Light
    Rleds[(5-z)+i*j].setRGB( 0, 0, 0);
    Rleds[(14+z)-i*j].setRGB( 0, 0, 0);
    Rleds[(25-z)+i*j].setRGB( 0, 0, 0);
    Rleds[(34+z)-i*j].setRGB( 0, 0, 0);
    Rleds[(45-z)+i*j].setRGB( 0, 0, 0);
   
    FastLED.show();
}
}//End of indicatorOn

//lightsOff
void lightsOff(){
  for (int i = 0; i<NUM_LEDS;i++){
  Rleds[i].setRGB( 0, 0, 0);
  Fleds[i].setRGB( 0, 0, 0);
  FastLED.show();
  }
} //End of lightsOff

//brakeLight
void brakeLight(int k){
  FastLED.setBrightness(k);
  for (int i = 0; i<NUM_LEDS;i++){
  Rleds[i].setRGB(255, 0, 0);
  FastLED.show();
  }
}//End of brakeLight

//headLightOn
void headLightOn(int k){
  FastLED.setBrightness(k);
  for (int i = 0; i<NUM_LEDS;i++){
  Fleds[i].setRGB(255, 255, 255);
  FastLED.show();
  }
}//End of HeadLightOn

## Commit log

2018-10-21 Create boardArduino
2018-11-01 Update Code/boardESP32/imPulseMain.ino
    - Beam light does not flicker when a street light is approached
    - Increased brightness
    - LDR range is now less sensitive
    - Many functions have been optimised using FastLED embedded libraries
